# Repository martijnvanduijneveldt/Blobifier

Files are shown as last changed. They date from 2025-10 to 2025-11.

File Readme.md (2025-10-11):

## Carrot Collective Projects

[ERCF v3](https://github.com/Carrot-collective/ERCF_v3)

[ERCT / CottonTail](https://github.com/Carrot-collective/ERCT)

[Filametrix Toolhead Cutter Buffer](https://github.com/Carrot-collective/Filametrix)

[Blobifier Purge System](https://github.com/Carrot-collective/Blobifier)

[Filamentalist Rewinder Buffer](https://github.com/Carrot-collective/Filamentalist)

### Carrot Collective Affiliates

[Jabberwocky Toolhead](https://github.com/kinematicdigit/Jabberwocky)

[Happy Hare Wiki](https://github.com/moggieuk/Happy-Hare/wiki)

<br />

Blobifier Render
Do you like the Blobifier? Consider [buying me a coffee](https://www.buymeacoffee.com/dendrowen) or support me through [paypal](https://www.paypal.com/donate/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)

# 1. What is it?
The Blobifier is a small device that eliminates the need for a purgeblock, making filament swaps more quick. It does this by extruding filament onto a tray creating a blob that will get ejected into a purge-bucket.
## 1.1 Features
- Turn your filament purge waste into blobs for fewer waste and quicker purging.
- Store the blobs in a bucket that can hold **400 blobs!** (for the V2 300mm version)
- Automatically pause the printer once the bucket is full.
- Detect when the bucket is installed or missing.
    - NOTE: Empty the bucket if you remove it! The system will reset the blob counter.
- Shake the bucket for better dispersion of the blobs in the bucket.
- Clean your nozzle on a brass brush before resuming to print.

Blobifier Render

Blobifier Video (https://www.youtube.com/watch?v=VNMafOdnZ84) Blobifier Video (https://www.youtube.com/watch?v=a73EYLjRkbQ)

# 2. Credit where credit is due
The Macro and Nozzle Scrubber are based on a version madde by by Hernsl (hernsl#8860 on Discord). 

# 3. Who is it for?
The device is designed around a Voron V2.4 300mm, but should work for 250mm and 350mm too. This version only supports the assembly on the rear-left of the bed. If you decide to change all this, please consider contributing to the project by creating a pull request with the needed changes.

# 4. BOM
Complete kit at:
- [aliexpress - Seleadlab](https://s.click.aliexpress.com/e/_DCsTsHL)
- [aliexpress - Fysect](https://s.click.aliexpress.com/e/_opb6U3d)
    - Requires other .stl files. Linked in the product description!
- .stl files should be printed using default Voron settings
  
Parts:
- 3 x M3x8 shsc
- 1 x M3x25 shsc
- 3 x M3x8 fhcs
- 3 x M3 t-nut
- 1 x M2x6 shsc (For the servo pivot arm)
- 2 x M2x10 self tapping screws
- 5 x heat set inserts
- 1 x 10x30 aluminum strip
    - max 1mm thick
    - Make sure it's thick enough to dissipate the heat from the nozzle
    - If you have the 'old' 10x15 strip, print the proper tray to match it.
- 1 x SG90 or MG90 servo (and the included screws)
- 1 x omron D2F-5L sized micro switch. Any knock-off will work.
- 1 x brass brush
- 1 x 4-pin jst connector set (male + female)
- other connectors and wire to connect it to the board

# 5. Build instructions
## 5.1 Bucket
### 5.1.1 Printed Parts
- **Bucket_*.stl** (whichever suits your printer (and printbed))
- **\*_Shaker.stl** (whichever suits your toolhead)
- **\*_Shaker_Arm.stl** (whichever suits your toolhead)
    - The included **\*_Shaker_arm_poo.stl** can be used for a multimaterial print.
### 5.1.2 Assembly
1. Insert 4 heatset inserts in the arm. Mind that one needs to be inserted at an angle.
2. Screw the arm to the bucket with the *poo* being upright using 2 M3x8 fhcs screws.
3. Screw the shaker to the arm with the opening facing the bucket using an M3x8 fhcs and M3x8 shsc screw.

## 5.2 Brush
### 5.2.1 Printed Parts
- **Brush.stl**
### 5.2.2 Assembly
1. Cut off the handle from the brass brush and insert it into the printed part. If it doesn't fit smootly, file down the brush further until it does.
2. Screw the brush down on the left bed extrusion with the brush against the rear of the bed using an M3x8 shcs and t-nut.

## 5.3 Base
### 5.3.1 Printed Parts 
- **Base.stl**
- **Tray.stl**
- **Servo_arm_*.stl** (Check which arm fits properly on your servo)
- **Mount_*.stl** Check the mount for your printer. The V2.4 has two mounts because some beds are slightly wider(255, 305 or 355)
- **Base_shim.stl** The tray needs to be sligtly above the bed surface (Scale Z height of the object according to your needs. Keep in mind that the higher this part is, the longer the mounting screws need to be)
### 5.3.2 Assembly
1. Glue the piece of aluminum inside the tray. It might require a little force to make it slide into the cavity. Make sure the piece of aluminum is thick enough to dissipate heat from the nozzle without melting the plastic.
1. Sand down the tray untill the top and bottom are smooth. If the aluminum pertrudes the top a bit, sand that down with it.
1. Remove 3 included support from the base.
    - One in the slot for the tray
    - Two at the bottom for the switch and jst connector
1. Test fit the tray in the base. Slide it in from the back. It should stick out 15mm if fully inserted. If operation isn't smooth, go back to step 2.
1. Remove the tray from the base
1. Insert the servo from above making sure the wires face the cavity meant for them and are inserted first so they come out from the bottom. It could be a tight fit, but if your printer is properly tuned you shouldn't have any trouble. Make sure you inserted it fully, you can check from the bottom.
1. Insert the microswitch in the bottom. Check if the lever is correctly oriented. Screw it down with 2 M2x10 self tapping screws. The screw holes might be hard to see, because there is an extra layer for printability.
1. Insert the 4-pin female JST connector iside the slot. If the fit is very loose, use some glue. 
1. Solder the wires from the servo and the switch to this connector. The order is less important, just keep in mind that you'll have to connect the wire to the board in the same order.
    - pin 1: VCC (Red, usually)
    - pin 2: 
        - GND from the servo (Brown, usually)
        - C from the switch (pins are marked C, NC and NO)
    - pin 3: Signal wire from servo (Orange, usually)
    - pin 4: NC from the switch
1. Connect the base to your printer with a cable of your own making. You can drill a hole in the bottom plate of your printer to feed the wire through. **Be careful not to hit any components in your electronics compartment and ALWAYS unplug your printer from the wall if you're working on the electronics!** You'll have to pick empty pins on your board. Refer to your boards documentation on which pins to use.
    - pin 1: 5V (any 5V on your board should work)
    - pin 2: GND (any GND on your board should work)
    - pin 3: An output capable pin. Most of them are.
    - pin 4: A pin with an internal pullup resistor. Most of them have.
1. Insert a heated insert into the base mount. Only one side is suitable for it.
1. Slide the base in the mount and secure it with an M3x25 shsc.
1. Screw the base into place with 2 x M3x8 shcs and T-nuts onto the left 2020 extrusion. The tray should just slide behind your bed. You can temporarily insert the tray to verify the position.
1. Turn on your printer and include the config file found in the github. Then restart the klipper firmware.
1. run `BLOBIFIER_SERVO POS=out` in the console. You should hear your servo move.
1. Screw the servo arm onto the servo with the arm pointing towards the slot. Make sure you don't turn the servo while doing this. If you accidentally turn it, run `BLOBIFIER_SERVO POS=out` again and continue.
1. Insert the tray from the back until the hole in the servo arm becomes visible through the tray. Then screw it down with an M2x4 screw, then go back half a turn so the screw can rotate freely in the tray.
1. Test the servo a couple of times with `BLOBIFIER_SERVO POS=in` and `BLOBIFIER_SERVO POS=out`. The tray should be fully inside or outside the base. If not, try to determine why.
    - There may be too much resistance in the sliding mechanism.
    - You might have screwed the m2 screw too tight.
    - The values in the config might need adjustment (unlikely)
1. Push the switch on the base. A message that the bucket is placed should be on the screen. Then let go of the switch. A message that the bucket was removed should be on the screen.
1. Place the bucket and see if it still works. If not, the base might need slight adjustment towards the center.

# 6. Configuration
Refer to the config files comments to configure the macro to your desires.

For maximum integration with Happy Hare, make use of the [gcode pre-processing](https://github.com/moggieuk/Happy-Hare/wiki/Gcode-Preprocessing). Make sure to include `PURGE_VOLUMES=!purge_volumes!`

Add BLOBIFIER to the post_load sequence in mmu_macro_vars.cfg
`variable_user_post_load_extension   : "BLOBIFIER"`

That's it. The Blobifier will now automatically be called for a purge everytime you swap materials. Oh... don't forget to disable that filthy wipe tower.

# 7. Release notes
## version 1.5
- Purge with a pulsating (and occasionally, retracting) motion. This will prevent laminar flow from occuring and purge the old filament more quicly. (Up to 30% EXTRA filament saved!)
- Changed the blob calculation mode. The blob will now split into equal parts if it is too large (e.g. 2x85mm instead of 150mm + 20mm). This will eliminate/reduce the small blobs scattering over the buildplate.
- Due to the above changes, certain variables have been added and removed:
  - new:
    - `z_raise`: The total amount the nozzle should be raised during a blob. The value should be somewhere around `iteration_z_raise * max_iterations_per_blob - triangular(iteration) * iteration_z_change`
    - `z_raise_exp`: The rate at which the hotend reduces raising speed during a blob. `0.85` seems to be a good starting value.
    - `purge_length_maximum`: The maximum length of the entire purge. Use `max_iterations_per_blob * max_iteration_length`.
  - removed:
    - `iteration_z_raise`
    - `max_iterations_per_blob`
    - `iteration_z_change`
    - `max_iteration_length`
- Revised some parameter checks to work with the new Happy Hare version 2.7
- Add settings:
  - `shaker_arm_z` to allow for different bed/shaker arm heights.
  - `brush_accell` to be able to change the acceleration of the brush movement.
- Keep in mind I do not maintain the `SW Only Blobifier.cfg`
## version 1.4
- Add a safe descend mode. This makes sure the toolhead can get down to the tray without hitting your prints. (requires exlude objects enabled in your slicer)
- Change the tray to fit a 30x10x1mm aluminum strip. This will prevent the tray from sagging over time. (The old tray is still available for these that have the smaller aluminum piece)
## version 1.3
- Add BLOBIFIER_PARK for use in conjuntion with Happy Hare. Parking prevents oozing.
- Removed the retraction moves (apart from the initial one in BLOBIFIER_PARK)
- Add a dwell time to relieve pressure from the nozzle
## version 1.2
- Purge volumes are now extracted from the new Happy Hare tool map!
- It is now advised to use the 'variables' of Happy Hare branch in conjunction with this mod.
- Add support for wider beds (5mm extra width) ([#6](https://github.com/Dendrowen/Blobifier/issues/6))
- Persistent blob state! Values are saved across reboots
## version 1.1
- Now fits the MG90 servo too!
- Tray height reduced to accomodate for the MG90 servo.
- Base servo cavity expanded for fitting an MG90.
- Added a channel alongside the servo for wiring the microswitch.
- Improved servo arm and removed different fits.
- Included supports in the base for easier printing.
- Modified the macro so it temporarily restores the feedrate to 100%.
- Adjusted the part cooling options. You can now either set it to a desired speed, or don't change it at all.
- Added some simple validation in the config to prevent bad values for the parameters.
## version 1.0
- Designed from the ground up in Fusion 360.
- Changed the way the system mounts for easy adaptation.
- Hexagon pattern on the bucket floor! (For smoother distribution, and hexagons are bestagons).
- Change shaker shape to better fit the Stealthburner toolhead.
- Included supports in the mount and brim-ears for the bucket.
- Add chamfers to most edges.
## version 0.3
- Add the poo icon for multicolored prints.
- Add a shaker arm to the bucket which the SB can slide into.
    - Other toolheads may be added in future releases.
- Move the brush to the right.
- Increase bucket height to 23mm.
- Add ridges to the bucket floor to help spread the blobs.
- Add a micro switch to the base bottom to detect the bucket.
- Updated BOM to include hardware for the brush
- Increased the hight of the base by 0.2mm for more support to for the tray
## version 0.2 & 0.1
- I... started making release notes with version 0.3

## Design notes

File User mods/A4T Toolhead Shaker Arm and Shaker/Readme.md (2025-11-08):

# A4T Shaker Arm Mod

A modified version of the shaker arm and shaker to fit the A4T toolhead.

CAD

## Variations Against the Stealth Burner Shaker Design

1. One M3x8 SHCS screw is needed to mount the shaker on the shaker arm.  
2. The shaker and shaker arm have indentations to align themselves to each other and prevent the shaker from twisting on the shaker arm, removing the need for the second M3 screw.  
3. The shaker and shaker arm have been made slimmer in the X direction to ease clearance between the front left Z belt and the shaker when inserting and removing the bucket from the printer.

## Which version to pick

### Shaker
There are two versions of the shaker. Depending on your bed placement and overall z height of your blobifier you may get a better shaking "experience" with the Shaker_A4T_tighter_fit model. 

### Shaker arm
There are two versions of the shaker arm. If you experience the arm sagging with the normal version you can try the Shaker_Arm_A4T_flat_with_deck model.

| Normal arm | Flat with deck model |
|---|---|
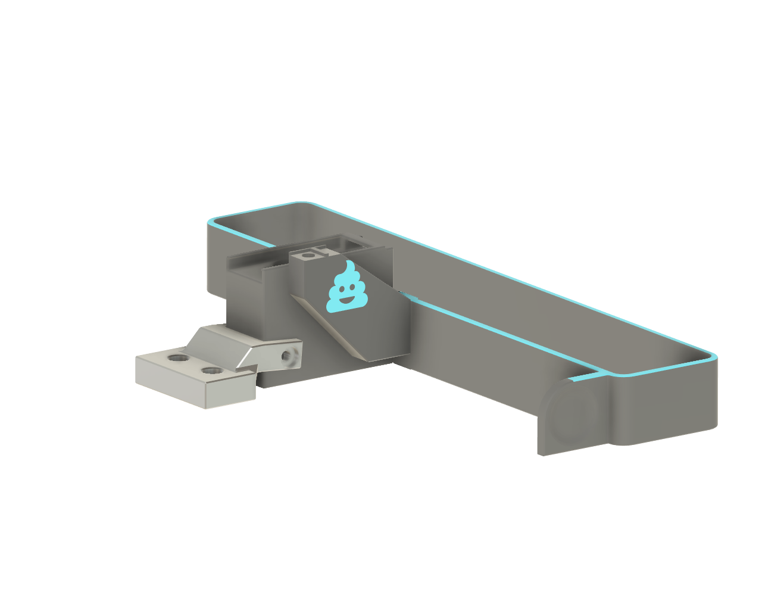
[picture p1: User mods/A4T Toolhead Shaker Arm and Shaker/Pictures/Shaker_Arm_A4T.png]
Normal arm
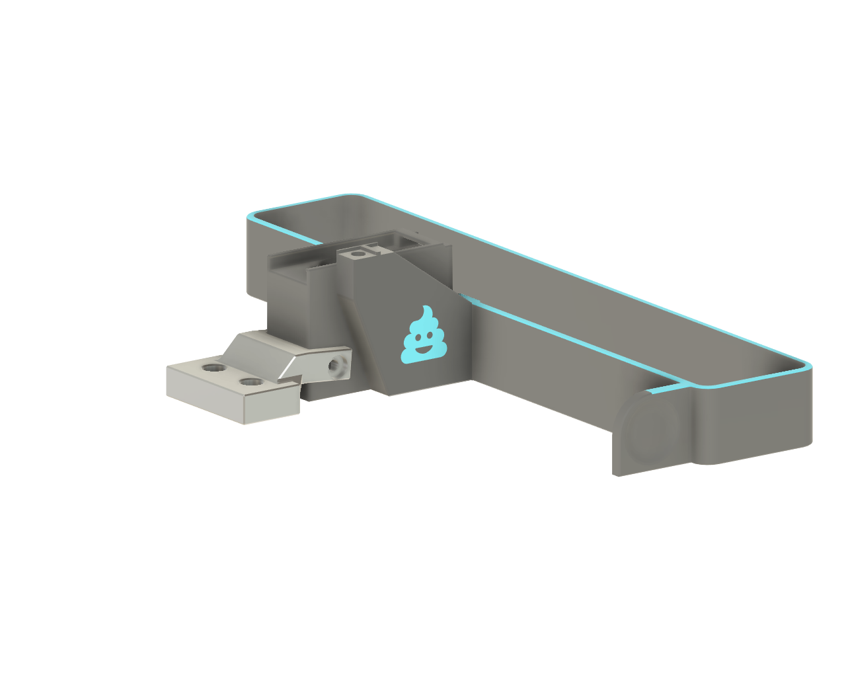
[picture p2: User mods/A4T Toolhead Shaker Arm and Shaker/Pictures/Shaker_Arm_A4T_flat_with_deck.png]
Flat with deck model
|  |  |

## Important configuration setup!

As the blobifier shaker arm sits above the plane of the bed, you have to ensure your minimum toolchange z height is adequate for the rear of the toolhead to clear the shaker arm when performing the cutting motion. 

As such, it is strongly advised to set it to approximately 15-20mm, (variable_min_toolchange_z : 15.0) to ensure no chance of collisions with the shaker arm and the mounting location of your bed probe at the rear of the toolhead.

## Bill of Materials (BOM)

### Printed Parts
- **Bucket_*.stl** (whichever suits your printer and print bed) – same as the Blobifier STL’s folder  
- **Shaker_A4T.stl**  
- **Shaker_Arm_A4T.stl**
Print using standard Voron part settings

### Hardware
- Same as the Blobifier. You won’t need the third M3x8 FHCS screw.



## Assembly

1. **Insert 3x M3 heat set inserts** in the shaker arm. Use an exacto knife or metal object to “level” the heat sets with the part, ensuring the inserts are flush with the surface of the arm and no excess material is oozing out.  
2. **Mount the arm to the bucket** (with the poo logo upright) using 2x M3x8 FHCS screws.  
3. **Align the shaker notches** to the arm and secure with the M3x8 SHCS screw.



## Calibration

Install and calibrate your shaker Z height as per the Happy Hare instructions.

- In a Voron 350, you might set `variable_shaker_arm_z` to `2mm`.  
- If the A4T is rubbing against the bottom of the shaker, increase slightly to `2.5mm` or `3mm`.  
- If using a beacon/cartographer or similar bed probe, it is recommended to set variable_min_toolchange_z : 15.0.

## Video

Watch the video (https://youtube.com/shorts/eVDUzT1yRBc)

Happy printing!

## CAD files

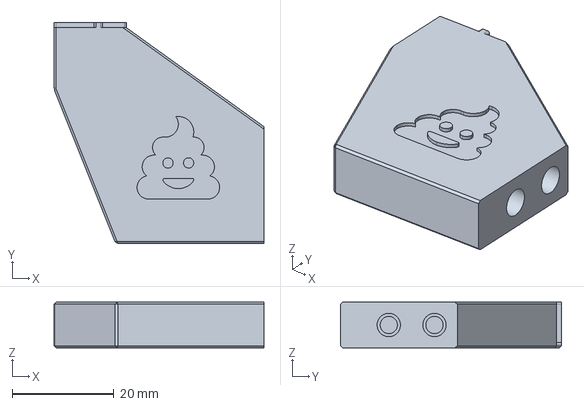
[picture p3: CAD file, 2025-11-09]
User mods/A4T Toolhead Shaker Arm and Shaker/CAD/Shaker_Arm_A4T_flat_with_deck.step
41.4 x 43.5 x 9.00 mm

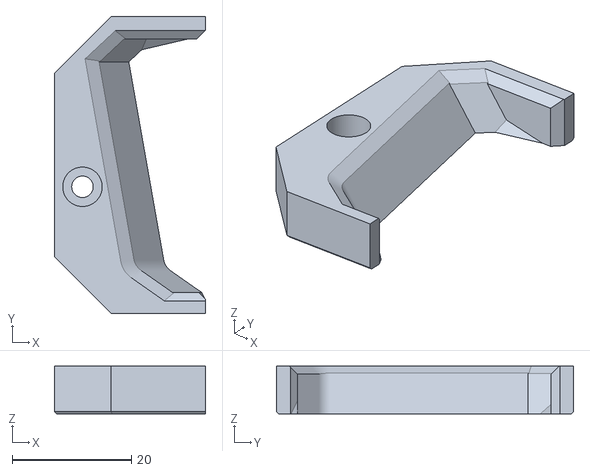
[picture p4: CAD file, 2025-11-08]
User mods/A4T Toolhead Shaker Arm and Shaker/STL/Shaker_A4T.stl
25.3 x 49.7 x 8.00

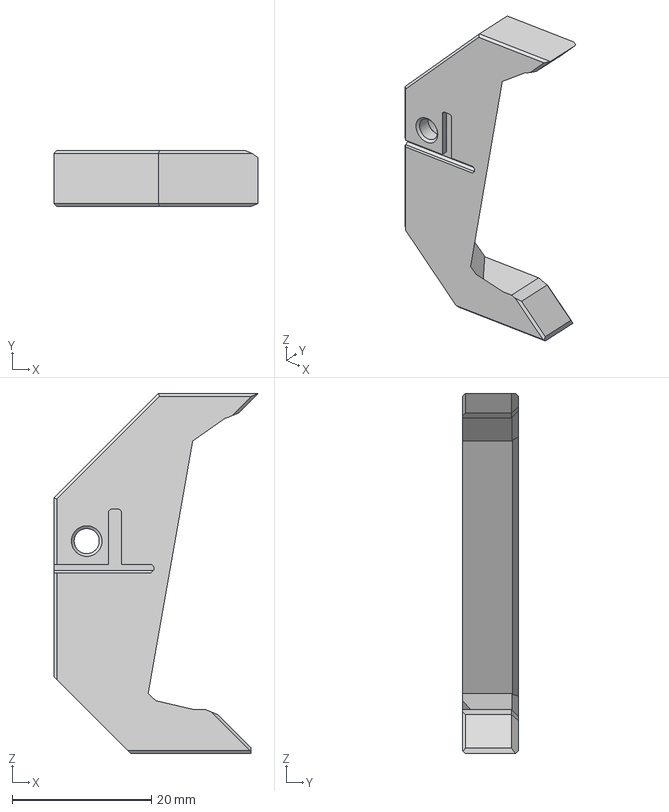
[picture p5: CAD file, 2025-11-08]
User mods/A4T Toolhead Shaker Arm and Shaker/CAD/Shaker_A4T_tighter_fit.step
29.3 x 8.01 x 51.7 mm

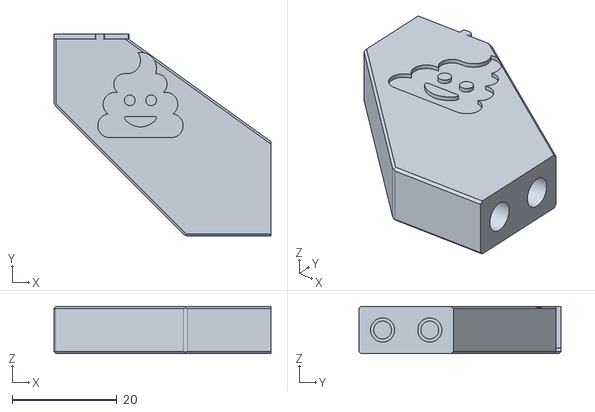
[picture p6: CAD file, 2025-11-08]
User mods/A4T Toolhead Shaker Arm and Shaker/STL/Shaker_Arm_A4T.stl
41.4 x 38.5 x 9.00

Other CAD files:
User mods/A4T Toolhead Shaker Arm and Shaker/STL/Shaker_A4T_tighter_fit.stl
User mods/A4T Toolhead Shaker Arm and Shaker/STL/Shaker_Arm_A4T_flat_with_deck.stl
